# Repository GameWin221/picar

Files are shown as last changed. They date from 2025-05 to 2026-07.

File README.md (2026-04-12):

# picar
Car with autonomous and remote-controlled capabilities controlled by Raspberry Pi 5 and a CH32V003 microcontroller. Features a custom made mainboard PCB responsible for controlling motors, servos and delivering power to the RPi 5.

It is capable of real-time remote control with a gamepad (e.g. XBox One gamepad) alongside a live WebRTC stream from its camera.
Moreover, simple autonomous driving is possible by following an RGB tracking marker.

### Version 3 Early (still the old frame from V2)

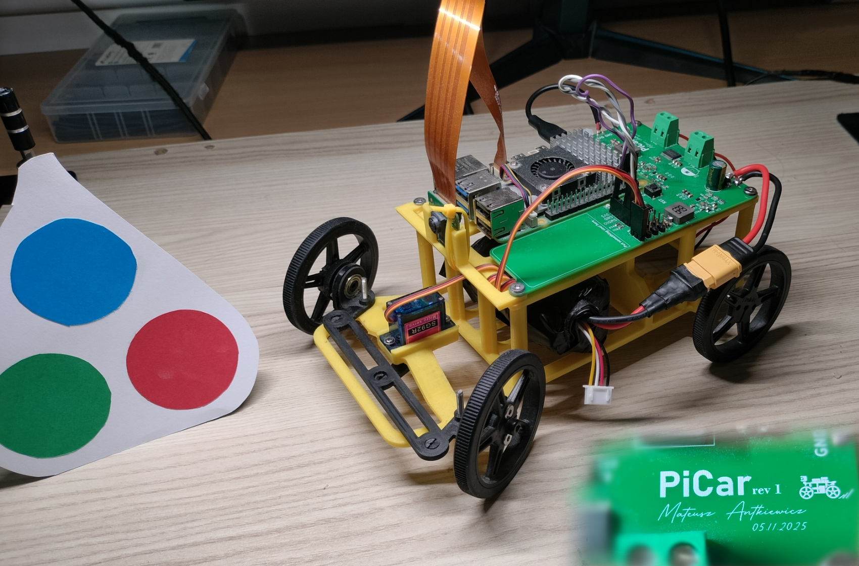
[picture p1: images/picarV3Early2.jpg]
picarV3early1

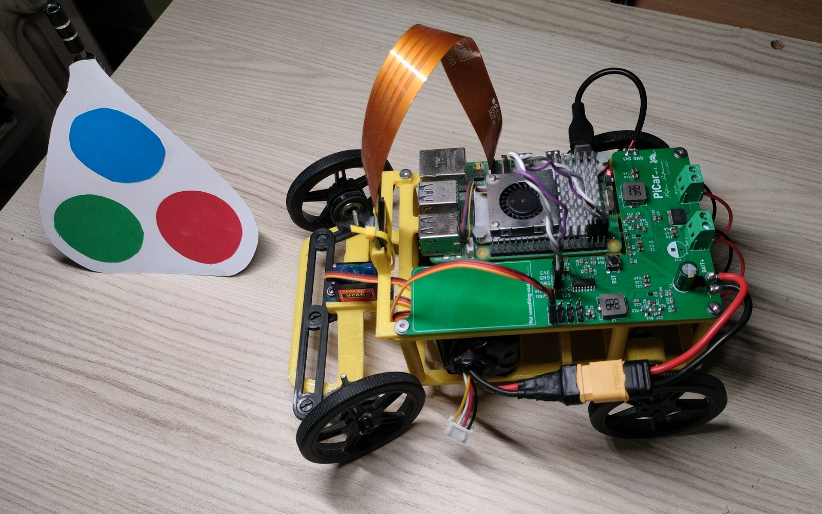
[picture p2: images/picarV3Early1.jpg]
picarV3early2


*PiCar with the tracking marker next to it*

## Future ideas 
- Add a ToF sensor and use it in tandem with the DepthAnything V2 depth estimation model to acquire real (approximated) depth information from the camera.

# Hardware
- Battery pack composed of 3x 18650 cells connected in series. It has both XT60 connector for the main power and 4-pin JST-XH used for balancing.
- SG92R micro servo used for steering
- Raspberry Pi 5 8GB
- Raspberry Pi Camera HD v2 8MPx
- Custom PCB mainboard responsible for controlling motors, servos and delivering power to the RPi 5. (More on that [below](#pcb-mainboard))
- Custom 3D-printed frame and steering system (files available in the "designs" directory)
- 4x 60x8mm black Pololu 1420 wheels
- 2x 6x13x5mm bearings for the front wheels
- 2x N20-BT07 micro 100:1 320RPM 12V motors
- M3 screws used for assembling the frame and wheels together

## PCB mainboard
schematic

*/pcb_main_board/pcb_main_board_schematic.svg*

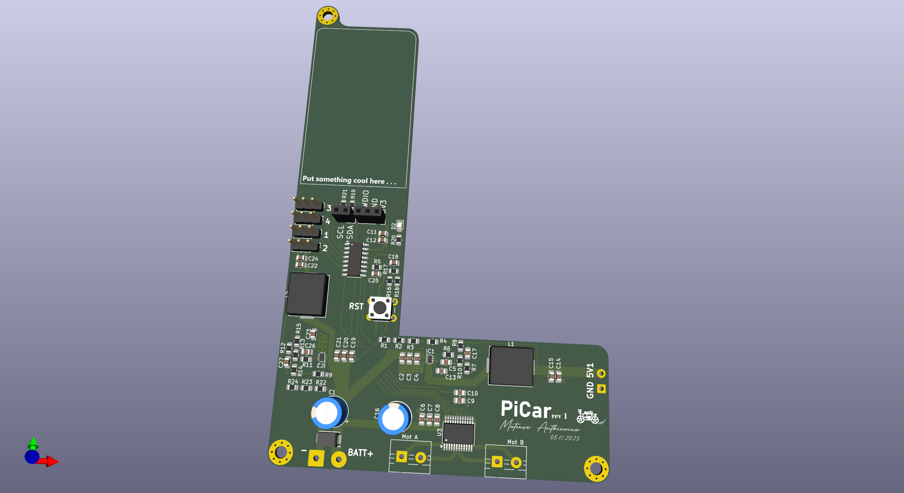
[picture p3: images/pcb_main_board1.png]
render


*/images/pcb_main_board1.png*

### On-board microcontroller

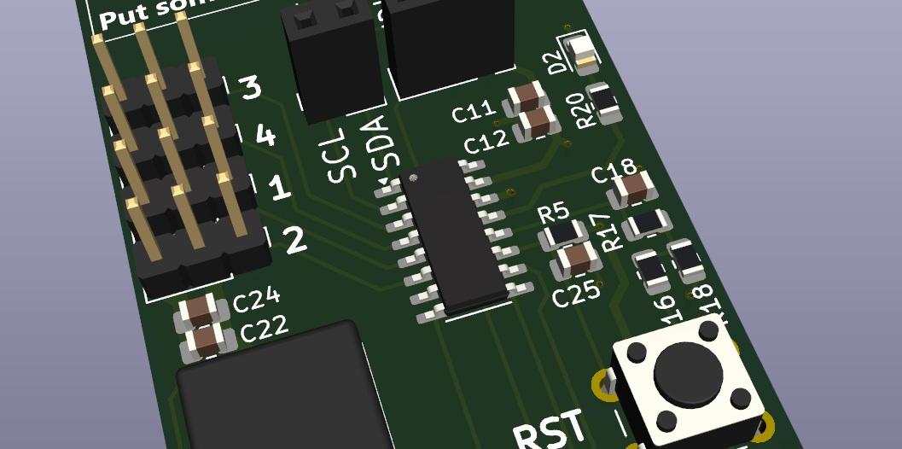
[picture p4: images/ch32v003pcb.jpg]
ch32v003


CH32V003 MCU is the main controller of the whole board. It is responsible for controlling the motor drivers, servo motors and monitoring the battery voltage. It communicates with the Raspberry Pi 5 over I2C.

### Battery to RPi 5 voltage step-down

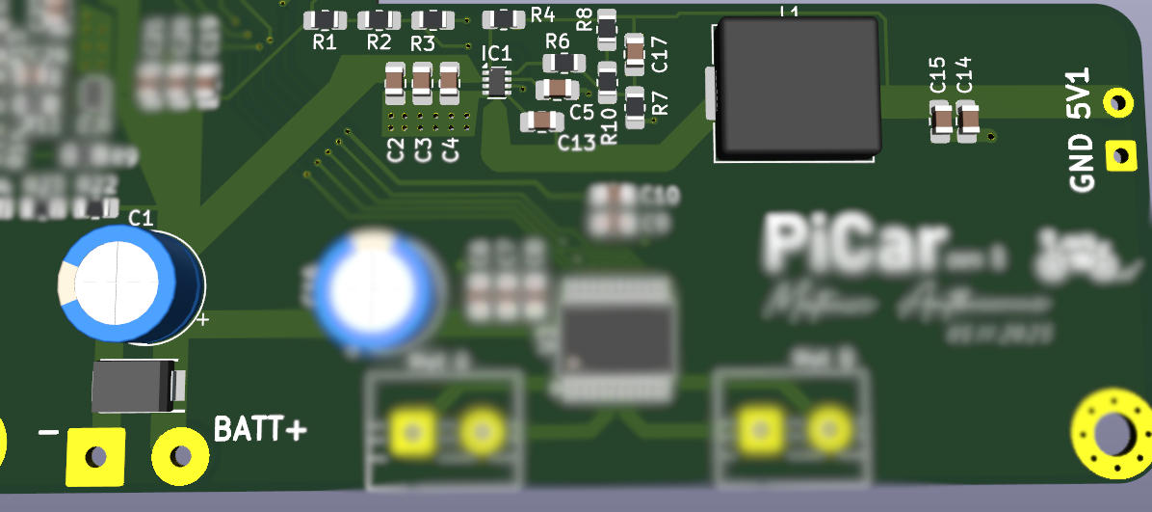
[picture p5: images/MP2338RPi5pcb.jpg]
mp2338


The battery input voltage is first filtered by the input low-ESR capacitor and capped to 15V by a SMBJ15A TVS diode. Then the MP2338 IC is used to reliably step-down the battery voltage from 9V-12.6V range to ~5.1V that is then connected via a USB-C cable to the RPi 5. The MP2338's GND pin is connected to wide copper traces with vias in order to improve cooling.

### Motor control

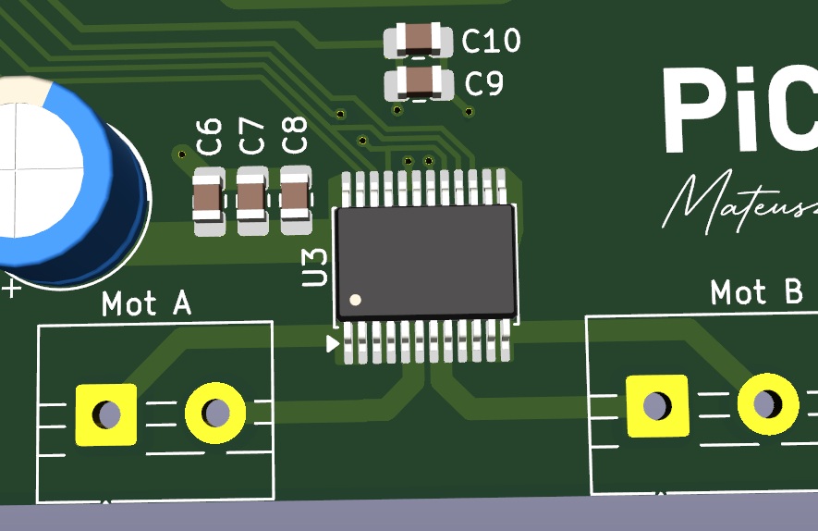
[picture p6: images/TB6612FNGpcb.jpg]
motors


TB6612FNG IC is used to drive both of the main motors. The IC logic is driven by PWM signals generated by the on-board microcontroller. The PWM frequency can be adjusted from the software layer if the user wants to prioritize peak power or to minimize the audible switching noise. The lower the frequency, the more efficient the motors are, but the louder they become.

### Servo control

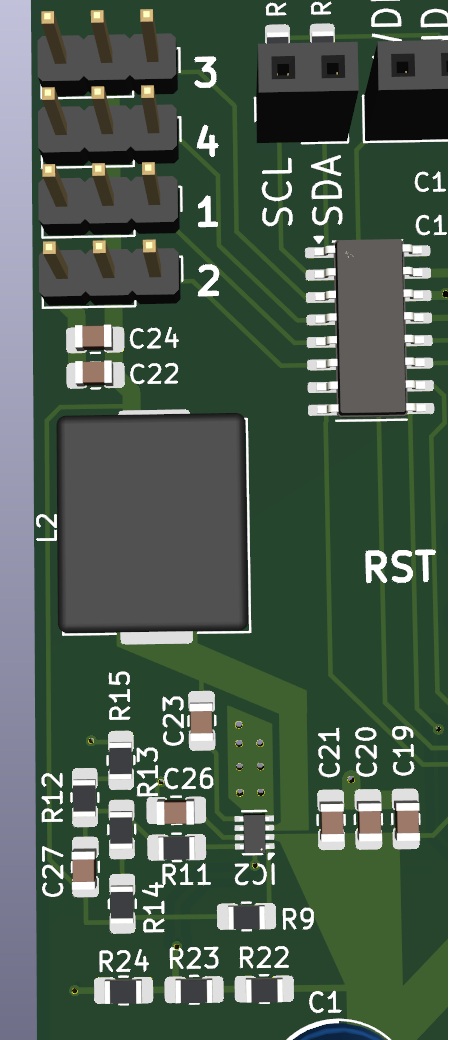
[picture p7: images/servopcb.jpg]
servo


The mainboard is capable of running 4 separate hardware PWM signals at once which are generated by the on-board microcontroller. The servo motors are powered with 4.8V generated by another MP2238 IC configured in the same way as the other one used for powering RPi 5, except for the output voltage. The servo section also has a 3-pin header for each signal channel in order to simplify the connections. There are more servo channels than are currently needed for future-proofing reasons. *e.g. allowing the camera to have adjustable yaw and pitch in the future.*

### Wheels

The front wheels are fastened to their mounts with short M3 screws. Those mounts then clip into the ball bearings, working similarly to LEGO Technic connections. A pin with the correct diameter and side cuts is pushed into the bearing hole and holds firmly enough for normal operation. The rear wheels are press-fitted onto the motor shafts:

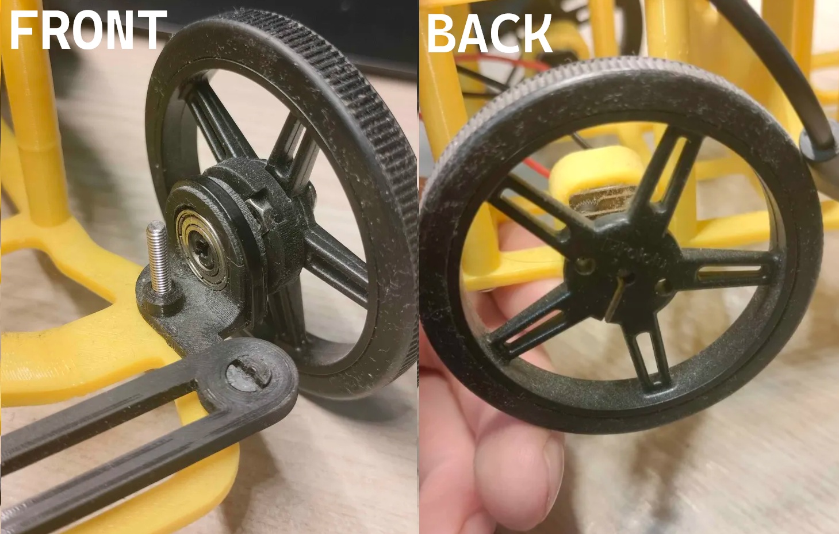
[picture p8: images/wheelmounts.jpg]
frontandback


Front wheel assembly disassembled in Fusion 360:

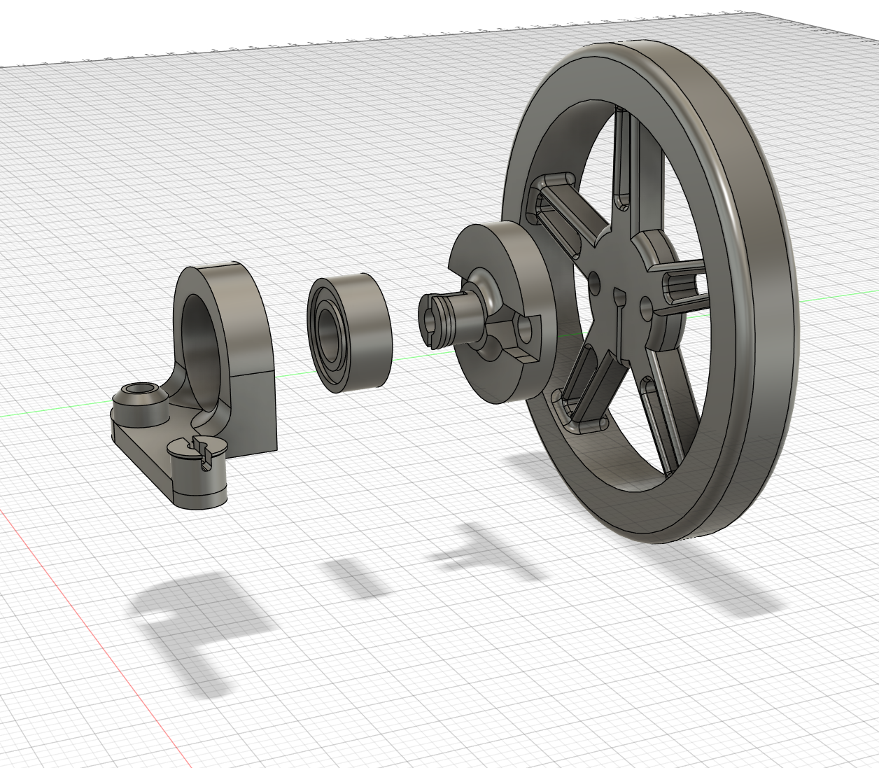
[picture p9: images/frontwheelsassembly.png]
frontwheelassembly


# Software and control

## Frontend
**PiCar** can be controlled through a simple Websockets-based web interface (`/car/software/index.html`). When you run the Python `"Remote Control" main loop` an HTTP server starts up and reveals the visual interface at `http://{raspberry_pi_5_ip}:8000`. There are two sliders that control it but the better (and way cooler) option is to **use a gamepad and control the car this way**. The website automatically detects connected gamepads and lets the user steer by using both triggers for accelerating and braking and the left thumbstick for steering. It is also possible to set the motors PWM switching frequency.

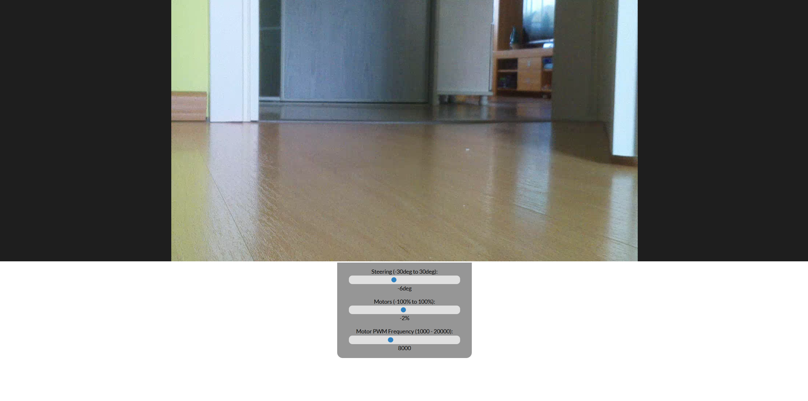
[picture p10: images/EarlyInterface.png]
frontenddemo


There also is a viewport for watching the live feed coming from the camera connected to the RPi 5. The stream source must be a WebRTC source which can be created easily by using [MediaMTX](https://github.com/bluenviron/mediamtx). You can find the working `mediamtx.yml` file I use to enable the stream at `/car/mediamtx.yml`. Once mediamtx starts with my provided config, the camera can be accessed by connecting via WebRTC to `{raspberry_pi_5_ip}:8889/rpi`.

## Vision

Autonomous driving, for now, is a simple computer vision algorithm that searches for a special marker with three key colors: red, green, and blue on the live feed streamed from the Raspberry Pi Camera HD v2 8MPx.

The camera feed is first filtered bilaterally to remove small details and noise in the subsequent marker search. Then gamma is adjusted to increase contrast, and the resulting image is binarized so that the SimpleBlobDetector from the OpenCV library can detect three circles. Finally, the algorithm checks whether the circles are "inside" the potentially found marker—i.e., whether they are not shifted from the averaged center by more than one standard deviation. If they are not, we can be certain that the marker has been found.

Below is a visualization of how the marker is seen by the algorithm:

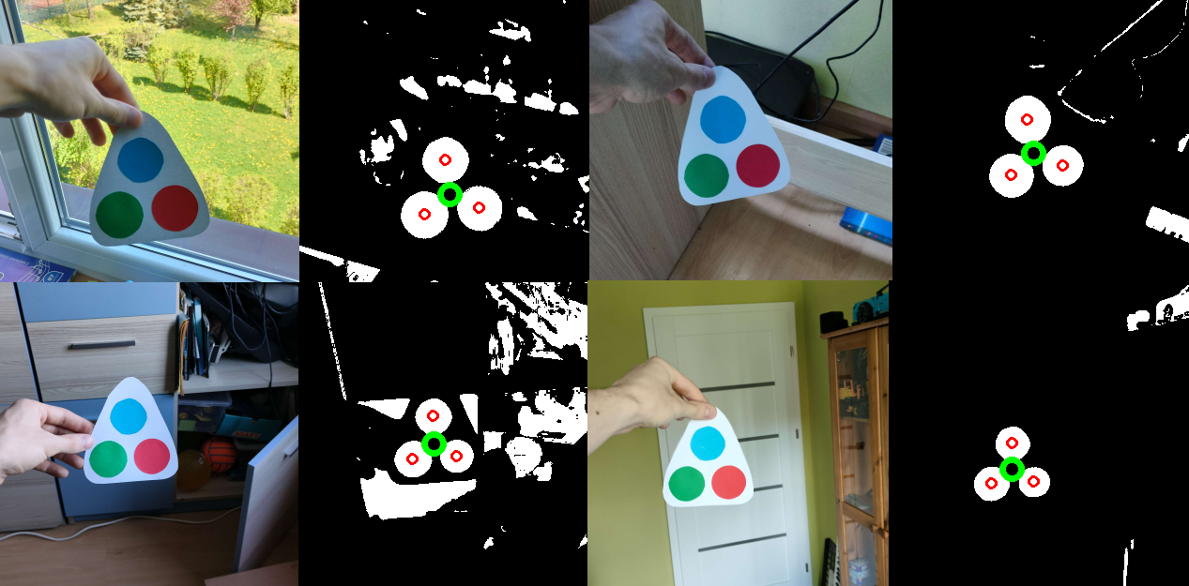
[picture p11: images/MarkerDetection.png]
MarkerDetection


When the marker is found, the vehicle drives forward and turns so that the center of the marker aligns with the center of the camera's view. This is sufficient to effectively track the marker.

### Future Vision Enhancement

I plan to use a ToF distance sensor in tandem with the computer vision model **DepthAnythingV2**, which estimates depth using a single camera. This combination will allow me to acquire approximate (yet sufficiently accurate) distance information of everything visible in the front camera. This data will enable shape detection by contours and autonomous obstacle avoidance.

## Firmware

The CH32V003 microcontroller runs a firmware that acts as a PWM and motor control interface for the Raspberry Pi 5. The firmware exposes a register-based interface over I2C using slave address `0x17`, allowing the RPi to elegantly control all aspects of motor and servo operation.

### I2C Communication Protocol

The firmware operates as an I2C slave that receives write-only commands structured as `[register_id, data_low, data_high]`. Each register controls a specific aspect of the system:

| Register | Purpose | Range |
|---|---|---|
| 1 | TIM1 (servo) frequency | 1 - 48000 Hz |
| 2 | TIM2 (motor) frequency | 1 - 48000 Hz |
| 4-7 | Servo CH1-CH4 duty cycle | 0 - PWM_PERIOD(1000) |
| 10-11 | Motor PWM (right/left) duty cycle | 0 - PWM_PERIOD(1000) |
| 12 | Motor direction control | Bit 0: DIRF, Bit 8: DIRB |

## Building the code

### RPi 5 Python
Configure the virtual environment if you need and run `pip install -r requirements.txt` while being in the `/car/software` directory to download the necessary packages. Downlaod opencv as a standalone package. Once everything is downloaded, run `python main.py` and it should work fine.

#### Enabling the necessary RPi 5 options
To make I2C communication work properly, enable it either with the `raspi-config` command or by manually adding the necessary lines to the `/boot/firmware/config.txt` file:

```
dtparam=i2c_arm=on
dtparam=i2c_arm_baudrate=80000 # or any other as you wish
dtparam=i2s=on
```

Also enable the camera detection in the same way. Here is the line for `/boot/firmware/config.txt`:

```
camera_auto_detect=1
```

### CH32V003 C Firmware
Downloading and building it through MounRiver Studio IDE is the easiest route to go. This repo already has project files that work out of the box when you open them with the IDE. Just press F7 and it should build perfectly fine.

#### Flashing it
You'll need a **WCH LinkE** programmer in order to flash the firmware to the chip. Once you have it, connect GND to GND and the SWDIO pin to the chip's SWIO pin according to its datasheet *(It's pin PD1 for CH32V003A4M6)*. The chip must be powered either from the programmer's voltage pin or externally during flashing.

Now go to MounRiver Studio IDE and press F7 to build your project and then F8 to flash it having the WCH LinkE programmer plugged into your computer at the same time, **note that flashing your code does not rebuild it automatically, you have to remember to press F7 each time.**. You can also change the flashing configuration but it's almost always good to go by default. *(called Download Configuration)*:

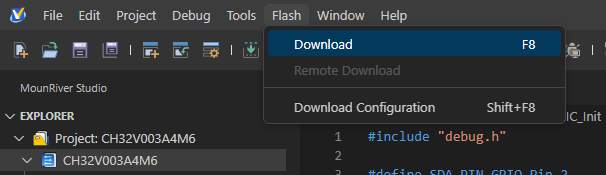
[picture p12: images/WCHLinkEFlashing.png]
wchlinke


Do not press or hold the reset button during flashing (the NRST pin)

# Archive

Take a look at the [PROGRESS.md markdown file](/PROGRESS.md) to see how the project evolved over time.

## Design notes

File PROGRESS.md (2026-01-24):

# Progress over time

## V3 (November 2025 / January 2026)

picarV3early1
picarV3early2

**You can read about it in the main README for as long as it is the newest version.**

## V2 (August 2025)

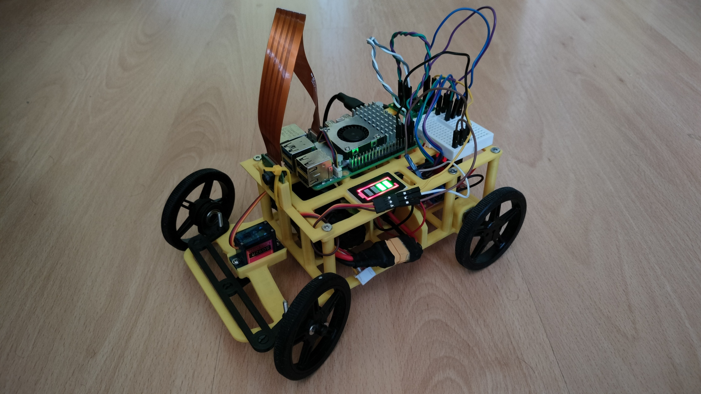
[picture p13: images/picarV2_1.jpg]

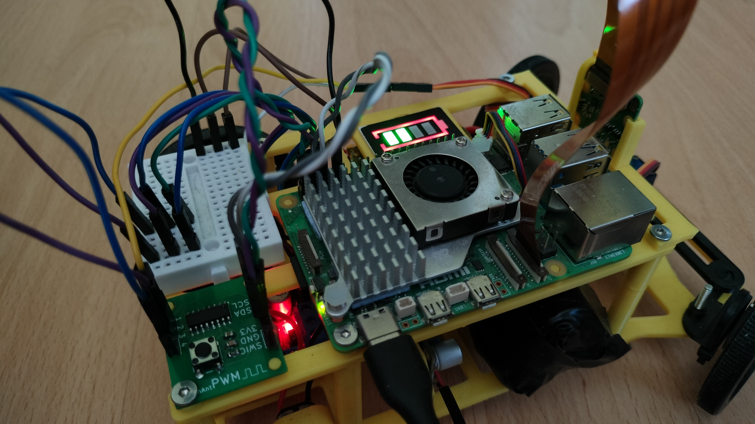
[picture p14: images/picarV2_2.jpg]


### Hardware
- [...] Same as V1 except for:
- Custom PWM control board based on CH32V003 (More on that [below](#ch32v003-mantpwm-pwm-board))
- A small breadboard used only for making the jumper wire connections easier to manage for now. *(I will get rid of it eventually because it doesn't look good)*

### CH32V003 "mAntPWM" PWM Board

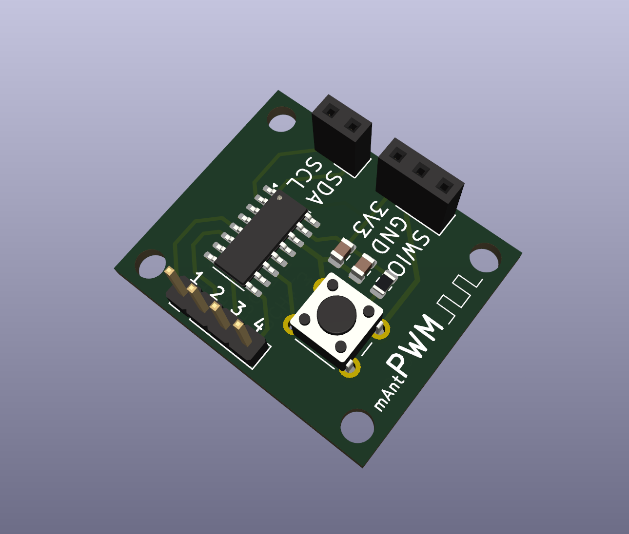
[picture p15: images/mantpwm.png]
mantpwm


*(The KiCad design files are in the `/pwm_board/design` directory)*

The board was designed and created to improve the PWM signal management. Raspberry Pi 5 itself was not enough because it can handle only 2 hardware PWM channels and I needed at least 3 channels so creating the board was both a solution to this problem and a cool sub-project to work on. Before making this board I came up with a temporary solution which you can read about [below](#saving-up-on-pwm-channels-before-the-pwm-board). 

Now I can see some flaws in the design such as wasted PWM outputs (I could've had up to 8 outputs instead of 4) or no on-board pull-up resistors for I2C but the board works as intended so I won't be ordering any new designs for now. 

### RPi 5 <-> mAntPWM coomunication
The RPi 5 communicates with the CH32V003 chip via I2C using a simple protocol documented in `/pwm_board/firmware/CH32V003A4M6/User/main.c`. You can also understand it better by reading the control functions in `/car/software/pwm_board.py`.

## V1 (April 2025)

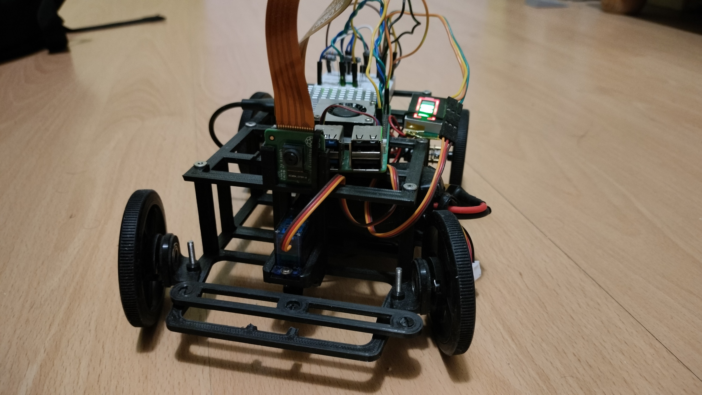
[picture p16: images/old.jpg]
v1pic1

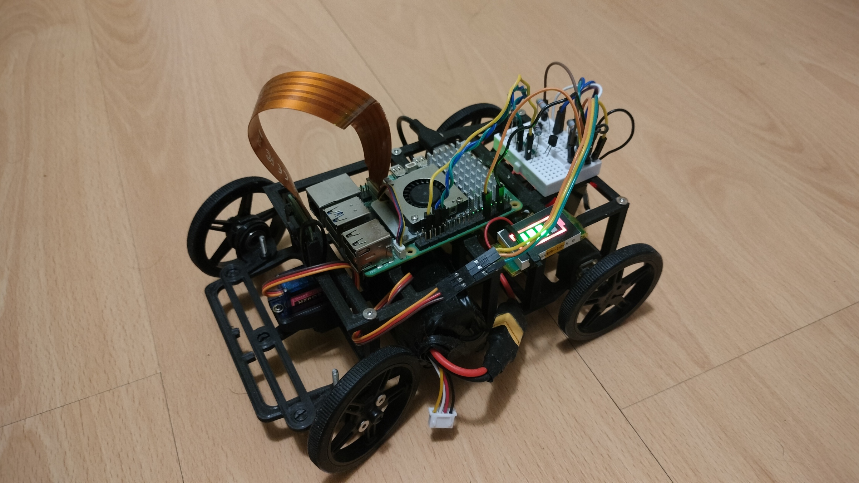
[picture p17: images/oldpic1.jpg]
v1pic2


### Hardware
- Powered by a custom made battery pack composed of 3x 18650 cells connected in series. It has both XT60 connector for the main power and 4-pin JST-XH used for balancing.
- SG92R micro servo for steering
- Raspberry Pi 5 8GB
- Raspberry Pi Camera HD v2 8MPx
- Custom PWM control board based on CH32V003 (More on that [below](#ch32v003-mantpwm-pwm-board))
- LM2596 step-down converter rated for 3A and set to (a bit more than) 5.1V used for powering the Raspberry Pi
- L298N motor driver used for motor control and for generating 5V powering the servo
- Cheap unnamed battery level indicator
- Custom 3D-printed frame and steering system (files available in the "designs" directory)
- 4x 60x8mm black Pololu 1420 wheels
- 2x 6x13x5mm bearings for the front wheels
- 2x N20-BT07 micro 100:1 320RPM 12V motors
- M3 screws used for assembling the frame and wheels together
- Breadboard with two BC337 transistors and required resistors.

### Saving up on PWM channels before the PWM board
Raspberry Pi 5 can generate only 2 channels of hardware PWM at once and I had to provide at least 3 PWM signals - one to control the servo, one for driving forward and one for driving backward. Since I didn't want to use software-based PWM I had to somehow cut down the number of signals. The obvious choice was to use only one PWM signal for the motors and to control the direction with digital outputs. I did it simply by switching the single PWM signal with two transistors going into separate inputs in the motor driver. 

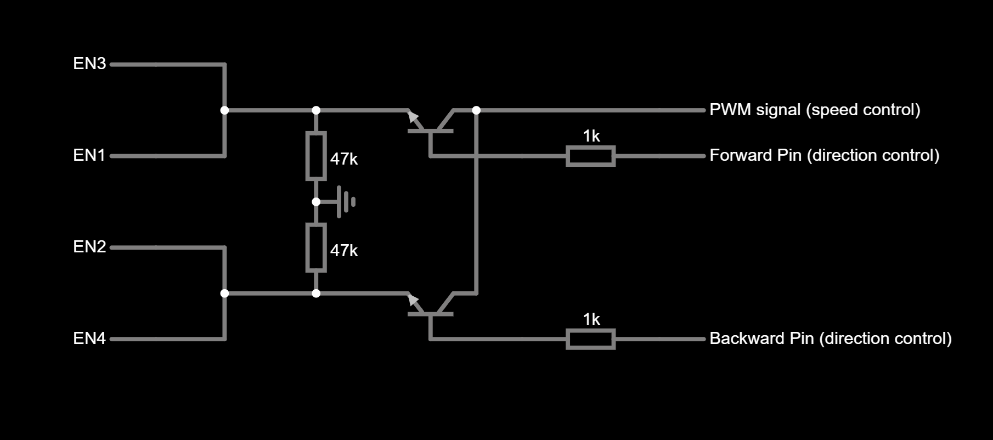
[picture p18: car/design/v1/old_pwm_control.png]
oldpwm


*Irl it was a messy setup on a breadboard as you can imagine.*

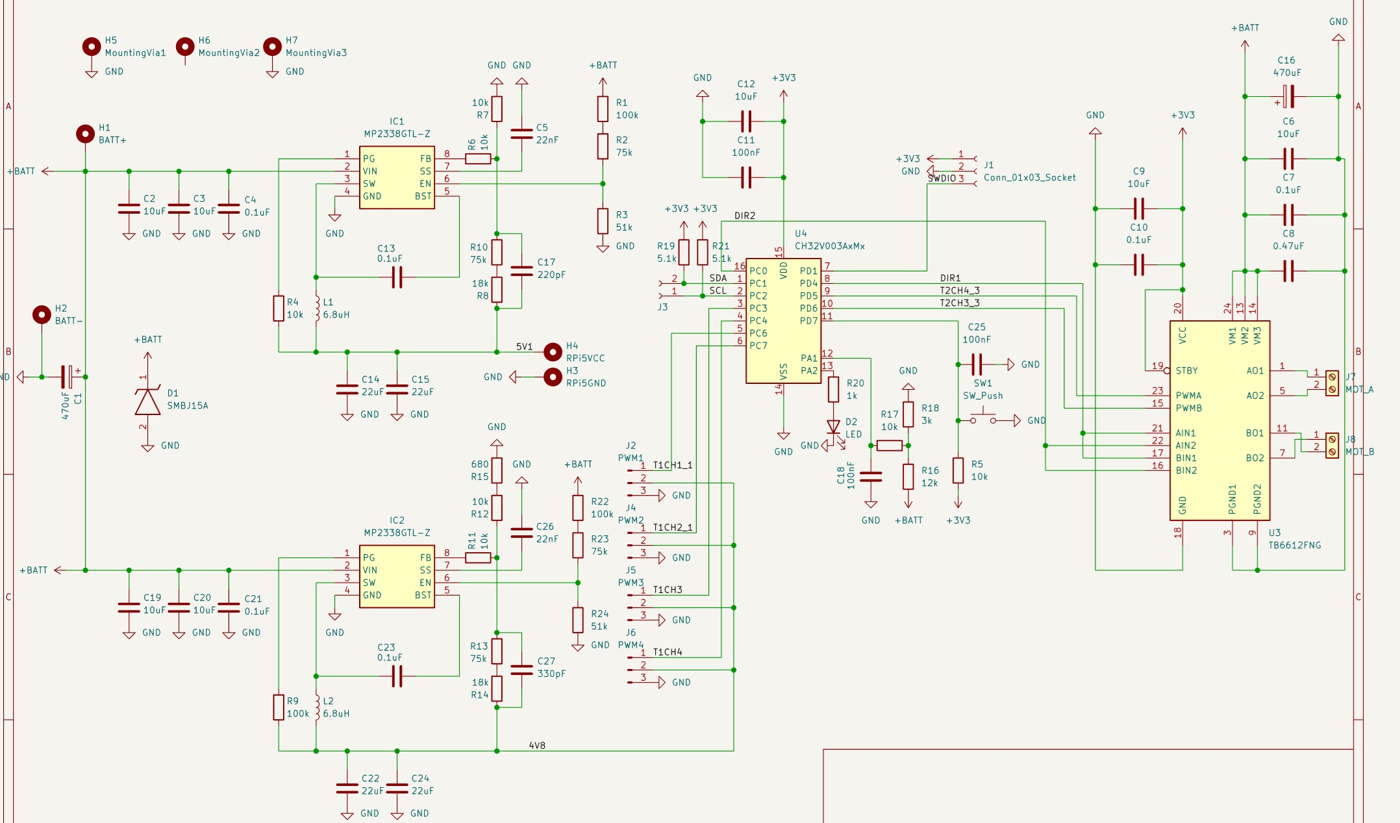
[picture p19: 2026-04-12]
images/schematicimage.jpg

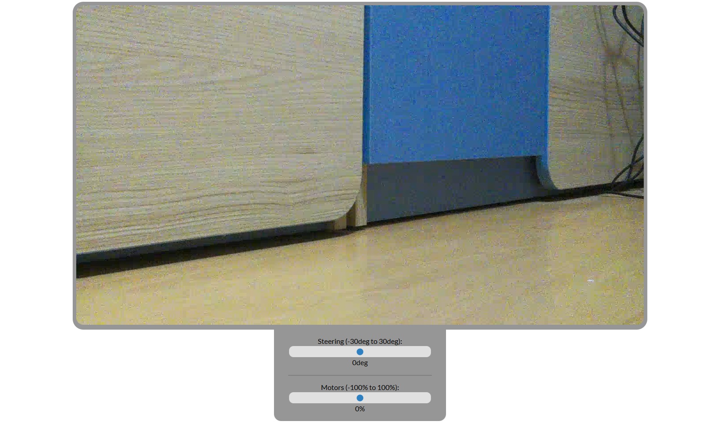
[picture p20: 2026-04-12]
images/WebInterface.jpg

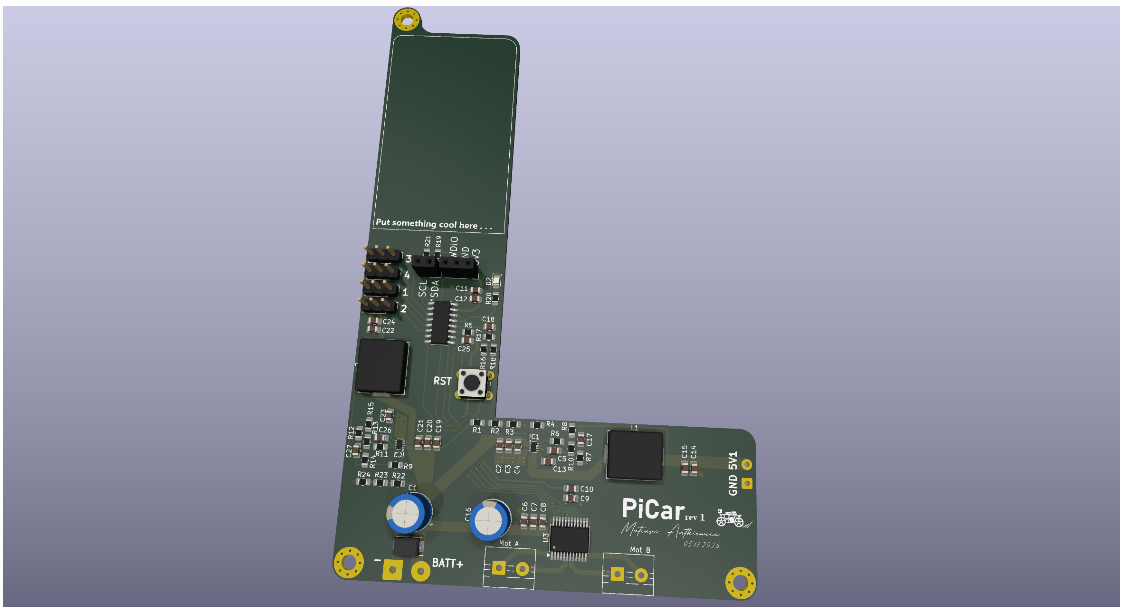
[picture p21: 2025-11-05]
images/pcb_main_board_rt1.png

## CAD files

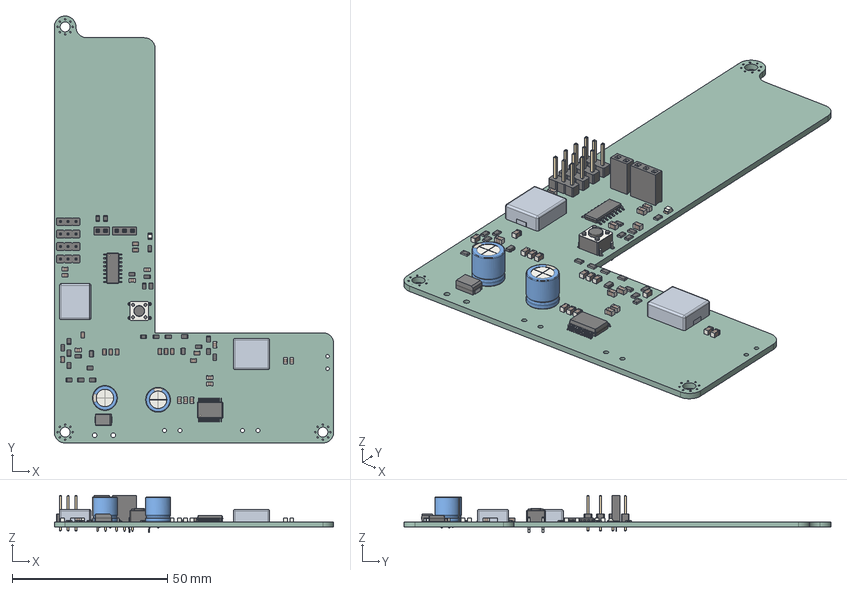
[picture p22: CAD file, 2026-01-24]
new_pcb_main_board/design/pcb_main_board.step
90.0 x 137.5 x 12.0 mm
C_0805_2012Metric x 25
R_0805_2012Metric x 24
CP_Radial_D8.0mm_P3.50mm x 2
PinHeader_1x03_P2.54mm_Vertical x 4
SW_PUSH_6mm
SOT-583-8 x 2
pcb_main_board 1.29.1 x 2
SSOP-24_5.3x8.2mm_P0.65mm
SOP-16_3.9x9.9mm_P1.27mm
FilletPin1
FilletPin2
PinSocket_1x03_P2.54mm_Vertical
LED_0805_2012Metric
PinSocket_1x02_P2.54mm_Vertical
pcb_main_board_PCB

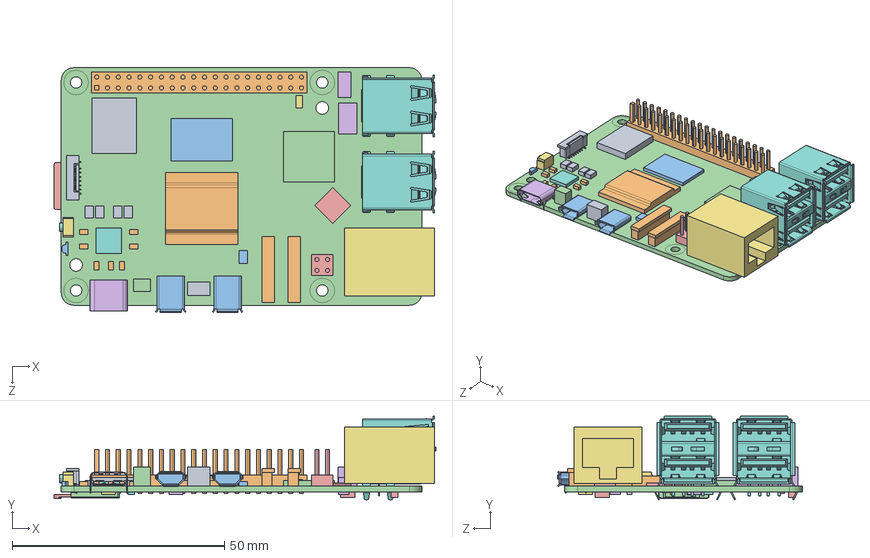
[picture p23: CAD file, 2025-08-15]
car/design/RaspberryPi5.step
90.0 x 19.8 x 57.7 mm
PCB_for REF 060923
GPIO Header for REF
Micro HDMI for REF x 2
SD CARD for REF
USB-C for REF
RJ45 for REF
USB for REF x 2
PCIe for REF
CAM-DISP for REF x 2
LED for REF
BAT Header for REF
PoE Header for REF
FAN Header for REF
SWITCH for REF
UART for REF

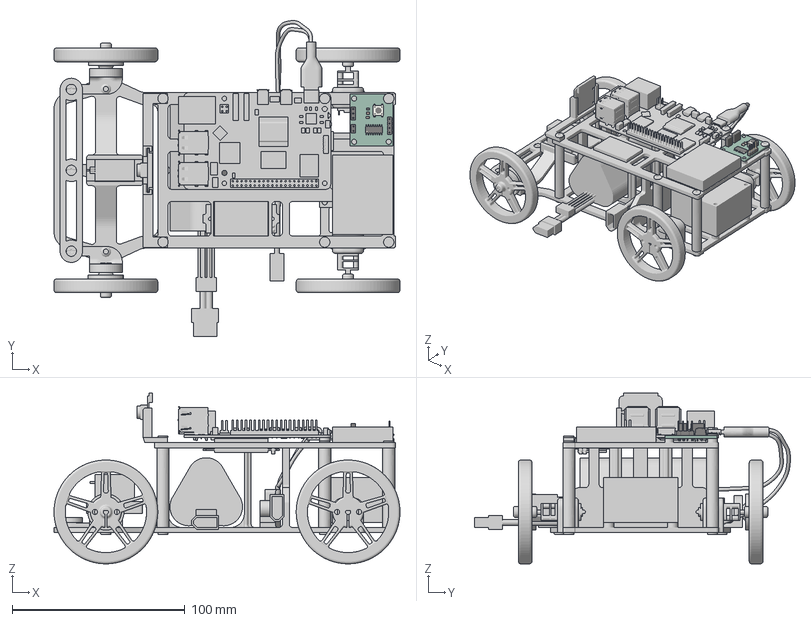
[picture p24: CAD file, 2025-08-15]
car/design/v2/picar.3mf
200.0 x 182.6 x 98.7 mm
Battery3S
BatteryDisplay
BearingFL
BearingFR
BottomFrame
Breadboard
Camera
CameraHandle
Driver
M3Screw1 (1) (1) (1) (1)
M3Screw1 (1) (1) (1)
M3Screw1 (1) (1)
M3Screw1 (1)
M3Screw1
M3Screw2 (1) (1) (1) (1)
M3Screw2 (1) (1) (1)
M3Screw2 (1) (1)
M3Screw2 (1)
M3Screw2
M3Screw3
M3Screw4
M3Screw5
M3Screw6
MotorBL
MotorBR
PowerCable1
PowerCable2
PowerConverter1
Servo
ServoArm
Standoff1 (1)
Standoff1
Standoff2 (1) (1)
Standoff2
Standoff3 (1)
Standoff3
SteerArmFL
SteerArmFR
SteerLinkage
TopFrame
USB_C_Connector
WheelBL
WheelBR
WheelFL
WheelFR
WheelMountFL
WheelMountFR

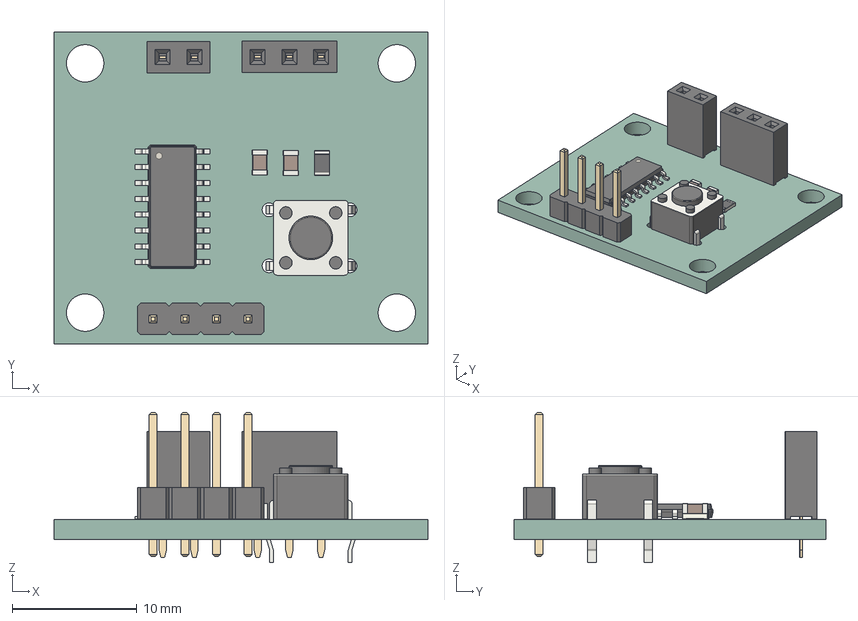
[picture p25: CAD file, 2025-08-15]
pwm_board/design/servo_controller.step
30.0 x 25.0 x 12.0 mm
C_0805_2012Metric x 2
PinSocket_1x02_P254mm_Vertical
PinSocket_1x03_P254mm_Vertical
PinHeader_1x04_P254mm_Vertical
SW_PUSH_6mm
SOP-16_3.9x9.9mm_P1.27mm
R_0805_2012Metric
servo_controller_PCB

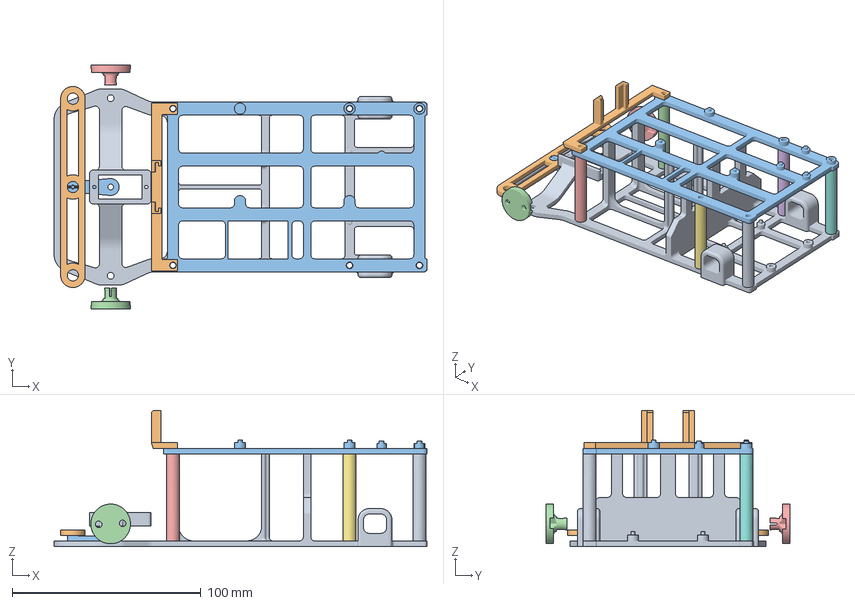
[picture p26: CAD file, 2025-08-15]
car/design/v2/picar_only_3d_printable.3mf
197.5 x 129.0 x 72.1 mm
BottomFrame
CameraHandle
ServoArm
Standoff1 (1)
Standoff1
Standoff2 (1) (1)
Standoff2
Standoff3 (1)
Standoff3
SteerLinkage
TopFrame
WheelMountFL
WheelMountFR

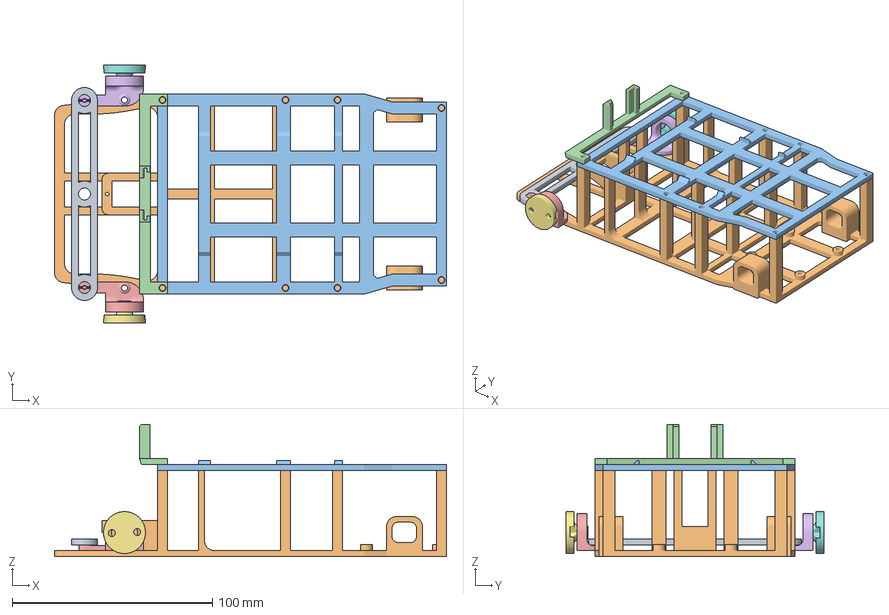
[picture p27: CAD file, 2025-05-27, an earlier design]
car/design/v1/picar_only_3d_printable.3mf
196.0 x 129.0 x 66.1 mm
SteerArmFL
SteerArmFR
WheelMountFL
WheelMountFR (1)

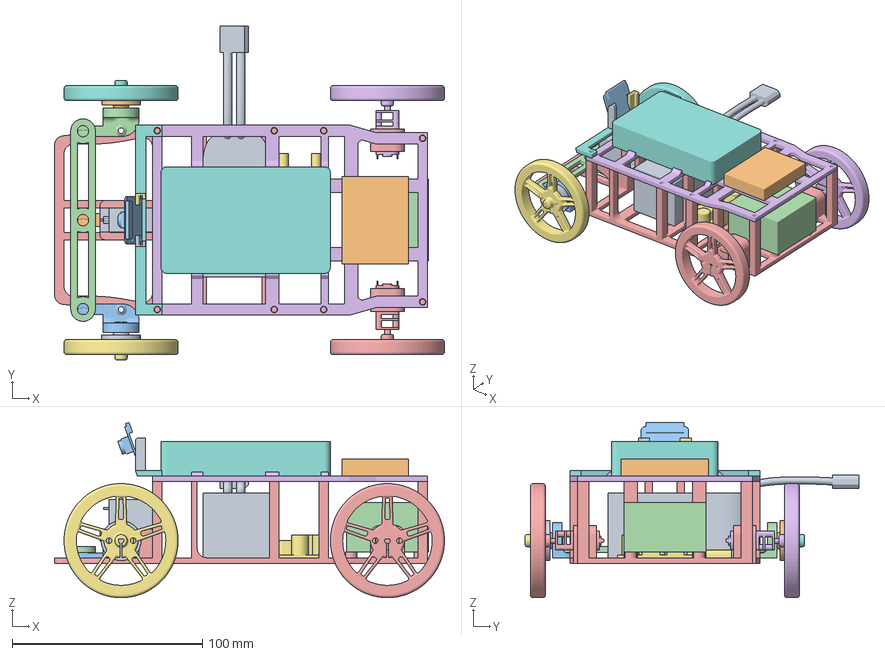
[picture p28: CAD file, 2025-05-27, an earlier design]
car/design/v1/picar.3mf
205.0 x 175.5 x 92.2 mm
Battery
BearingFL
BearingFR
Breadboard
Camera
Driver
MotorBL
MotorBR
PowerConverter (1)
RaspberryPi
Servo
ServoArm
SteerArmFL
SteerArmFR
WheelBL
WheelBR
WheelFL
WheelFR
WheelMountFL
WheelMountFR (1)

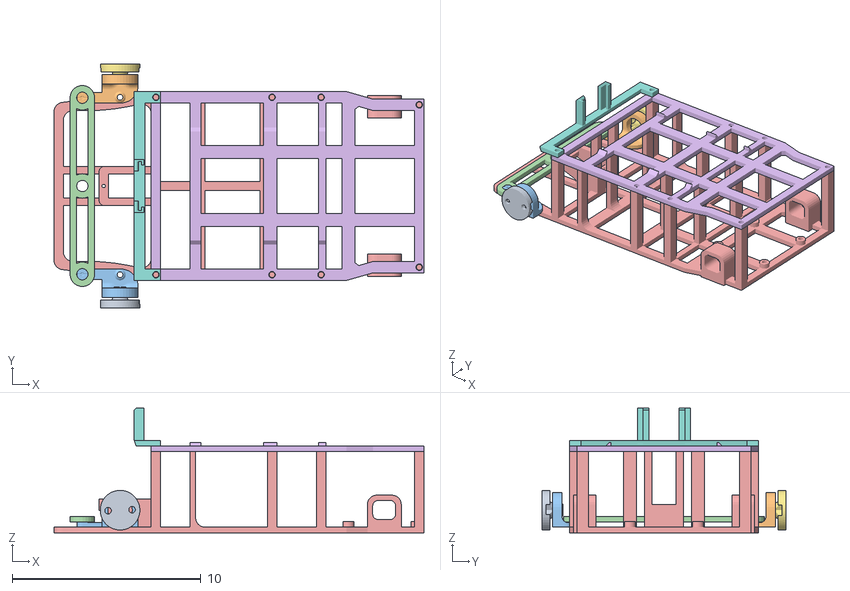
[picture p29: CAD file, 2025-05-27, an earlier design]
car/design/v1/picar_all_3d_printable.obj
19.6 x 12.9 x 6.61
WheelMountFL
SteerArmFR
SteerArmFL
WheelMountFR (1)

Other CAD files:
car/design/v1/picar.f3d
car/design/v1/picar.obj
car/design/v2/picar.f3d
car/design/v2/picar.obj
car/design/v2/picar_only_3d_printable.obj
new_pcb_main_board/design/pcb_main_board.stl

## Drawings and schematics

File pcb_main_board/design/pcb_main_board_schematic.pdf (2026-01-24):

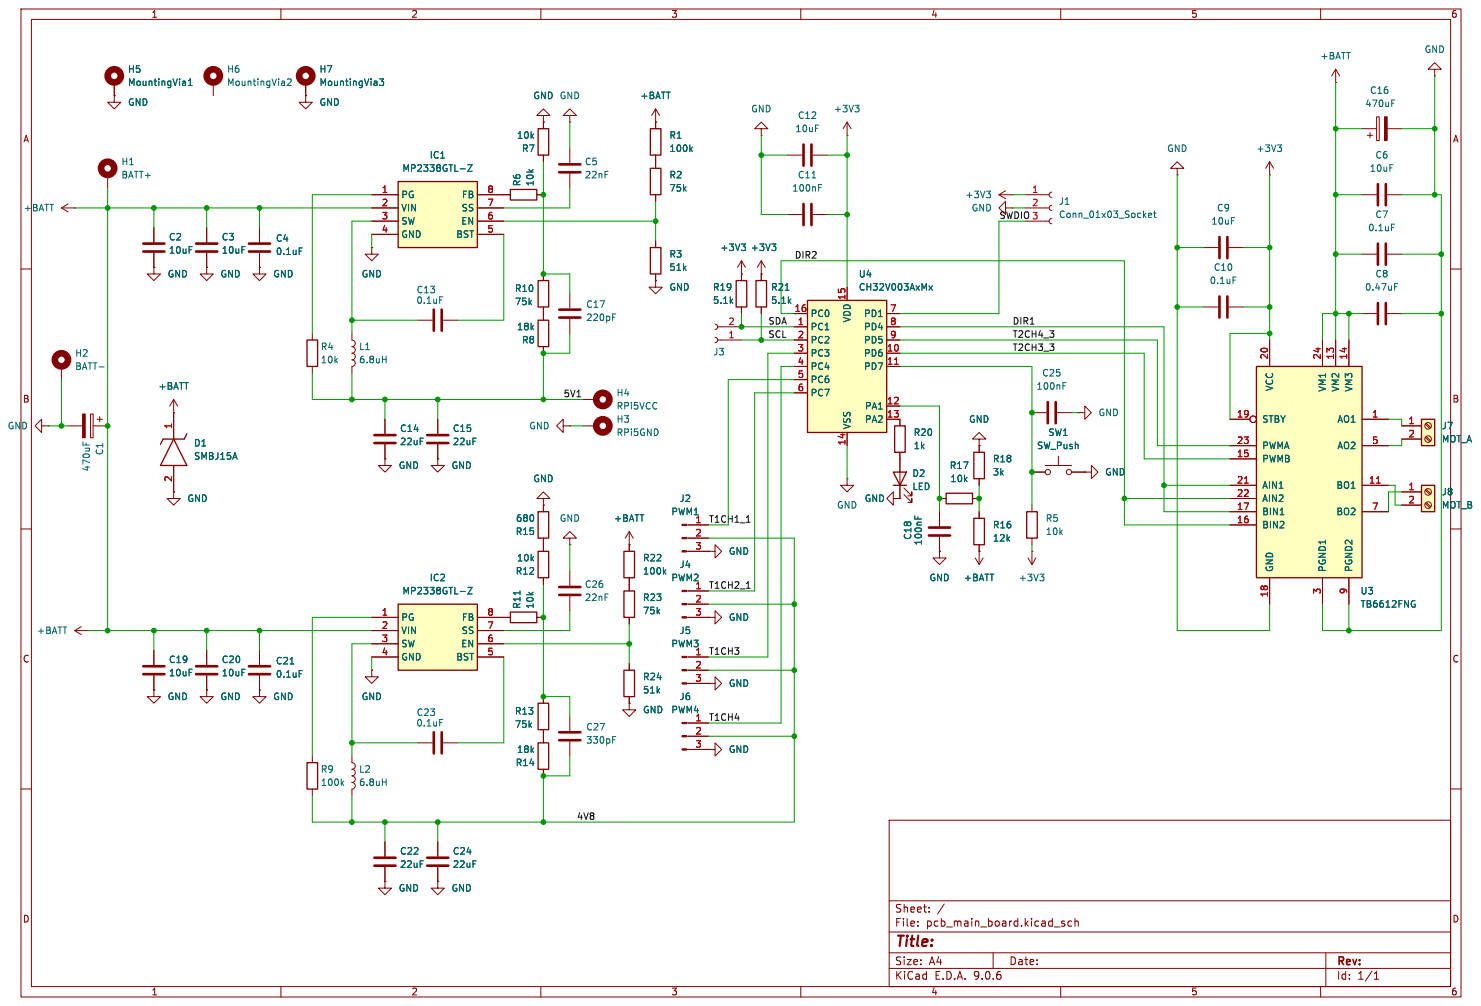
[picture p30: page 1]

Id: 1/1 Title: File: pcb_main_board.kicad_sch Sheet: /

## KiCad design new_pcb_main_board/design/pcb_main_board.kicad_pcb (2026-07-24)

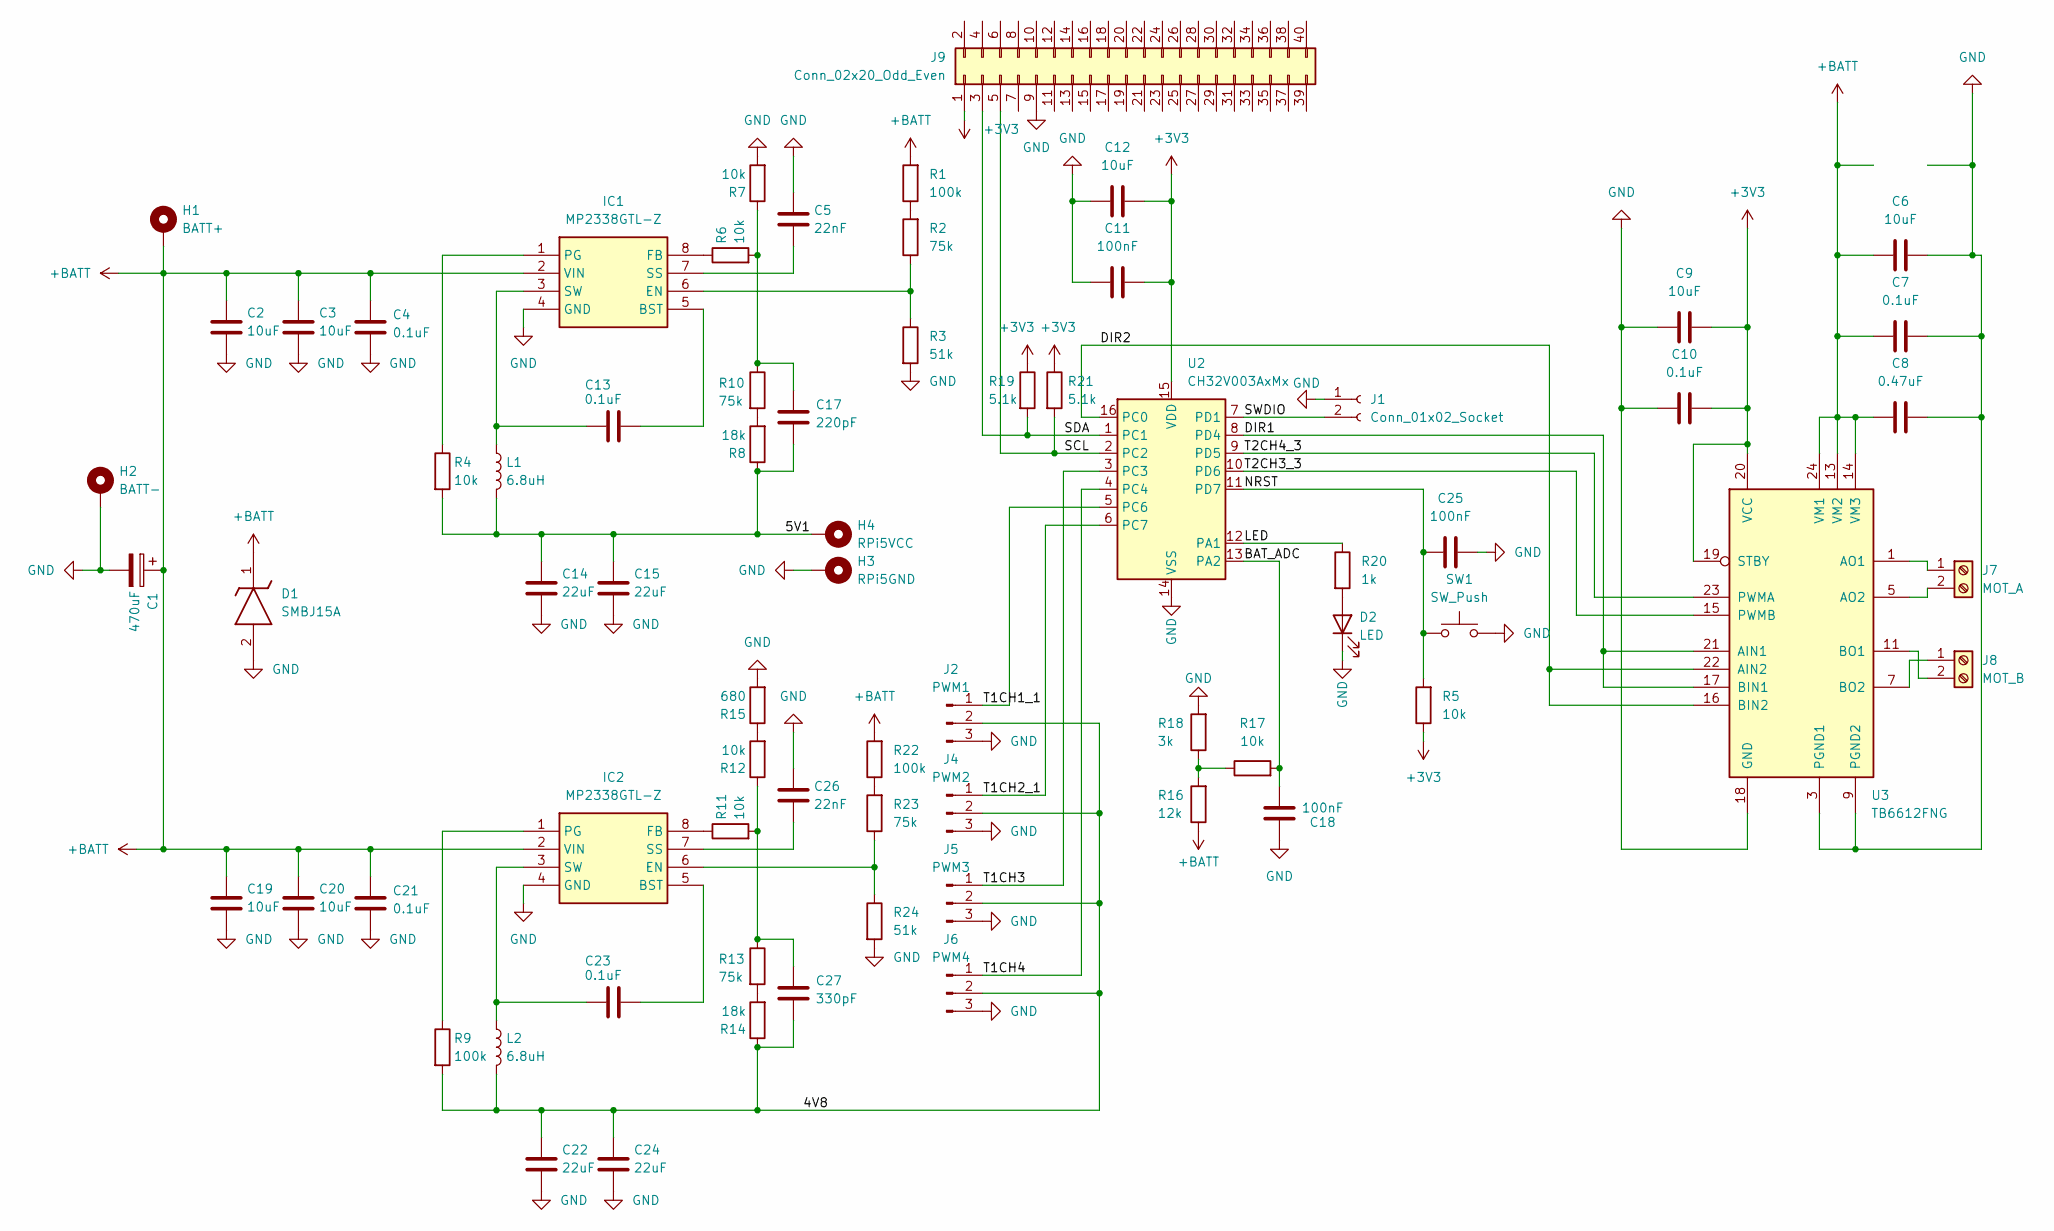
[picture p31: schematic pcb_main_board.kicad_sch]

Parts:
C1: 470uF; CP_Radial_D8.0mm_P3.50mm
C2, C3, C6, C9, C12, C19, C20: 10uF; C_0805_2012Metric
C4, C7, C10, C13, C21, C23: 0.1uF; C_0805_2012Metric
C5, C26: 22nF; C_0805_2012Metric
C8: 0.47uF; C_0805_2012Metric
C11, C18, C25: 100nF; C_0805_2012Metric
C14, C15, C22, C24: 22uF; C_0805_2012Metric_Pad1.18x1.45mm_HandSolder
C17: 220pF; C_0805_2012Metric
C27: 330pF; C_0805_2012Metric
D1: SMBJ15A; DIOM5436X244N; Mouser Part Number 78-SMBJ15A
D2: LED; LED_0805_2012Metric_Pad1.15x1.40mm_HandSolder
H1: BATT+; SolderWire-1sqmm_1x01_D1.4mm_OD3.9mm
H2: BATT-; SolderWire-1sqmm_1x01_D1.4mm_OD3.9mm
H3: RPi5GND; SolderWire-0.5sqmm_1x01_D0.9mm_OD2.3mm
H4: RPi5VCC; SolderWire-0.5sqmm_1x01_D0.9mm_OD2.3mm
IC1, IC2: MP2338GTL-Z; SOT-583-8; Mouser Part Number 946-MP2338GTL-Z
J1: Conn_01x02_Socket; PinSocket_1x02_P2.54mm_Vertical
J2: PWM1; PinHeader_1x03_P2.54mm_Vertical
J4: PWM2; PinHeader_1x03_P2.54mm_Vertical
J5: PWM3; PinHeader_1x03_P2.54mm_Vertical
J6: PWM4; PinHeader_1x03_P2.54mm_Vertical
J7: MOT_A; TerminalBlock_MaiXu_MX126-5.0-02P_1x02_P5.00mm
J8: MOT_B; TerminalBlock_MaiXu_MX126-5.0-02P_1x02_P5.00mm
J9: Conn_02x20_Odd_Even; PinSocket_2x20_P2.54mm_Vertical
L1, L2: 6.8uH; L_Chilisin_BMRF00101040
R1, R9, R22: 100k; R_0805_2012Metric
R2, R10, R13, R23: 75k; R_0805_2012Metric
R3, R24: 51k; R_0805_2012Metric
R4, R5, R6, R7, R11, R12, R17: 10k; R_0805_2012Metric
R8, R14: 18k; R_0805_2012Metric
R15: 680; R_0805_2012Metric
R16: 12k; R_0805_2012Metric
R18: 3k; R_0805_2012Metric
R19, R21: 5.1k; R_0805_2012Metric
R20: 1k; R_0805_2012Metric
SW1: SW_Push; SW_PUSH_6mm
U2: CH32V003AxMx; STC_SOP-16_3.9x9.9mm_P1.27mm
U3: TB6612FNG; SSOP-24_5.3x8.2mm_P0.65mm

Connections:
+3V3: C9.2, C10.2, C11.2, C12.2, J9.1, R5.1, R19.1, R21.1, U2.15 (VDD), U3.19 (STBY), U3.20 (VCC)
+BATT: C1.1, C2.1, C3.1, C4.1, C6.1, C7.1, C8.1, C19.1, C20.1, C21.1, D1.1 (K), H1.1, IC1.2 (VIN), IC2.2 (VIN), R1.2, R16.1, R22.2, U3.13 (VM2), U3.14 (VM3), U3.24 (VM1)
/4V8: C22.1, C24.1, C27.2, J2.2, J4.2, J5.2, J6.2, L2.2, R9.2, R14.1
/5V1: C14.1, C15.1, C17.2, H4.1, L1.2, R4.2, R8.1
/BAT_ADC: C18.2, R17.2, U2.13 (PA2)
/DIR1: U2.8 (PD4), U3.17 (BIN1), U3.21 (AIN1)
/DIR2: U2.16 (PC0), U3.16 (BIN2), U3.22 (AIN2)
/LED: R20.1, U2.12 (PA1)
/NRST: C25.1, R5.2, SW1.1, U2.11 (PD7)
/SCL: J9.5, R21.2, U2.2 (PC2)
/SDA: J9.3, R19.2, U2.1 (PC1)
/SWDIO: J1.2, U2.7 (PD1)
/T1CH1_1: J2.1, U2.5 (PC6)
/T1CH2_1: J4.1, U2.6 (PC7)
/T1CH3: J5.1, U2.3 (PC3)
/T1CH4: J6.1, U2.4 (PC4)
/T2CH3_3: U2.10 (PD6), U3.15 (PWMB)
/T2CH4_3: U2.9 (PD5), U3.23 (PWMA)
GND: C1.2, C2.2, C3.2, C4.2, C5.1, C6.2, C7.2, C8.2, C9.1, C10.1, C11.1, C12.1, C14.2, C15.2, C18.1, C19.2, C20.2, C21.2, C22.2, C24.2, C25.2, C26.1, D1.2 (A), D2.1 (K), H2.1, H3.1, IC1.4 (GND), IC2.4 (GND), J1.1, J2.3, J4.3, J5.3, J6.3, J9.9, R3.2, R7.2, R15.2, R18.2, R24.2, SW1.2, U2.14 (VSS), U3.3 (PGND1), U3.4 (PGND1), U3.9 (PGND2), U3.10 (PGND2), U3.18 (GND)
unnamed: C17.1, R6.2, R7.1, R10.1
unnamed: C27.1, R11.2, R12.1, R13.1
unnamed: D2.2 (A), R20.2
unnamed: C13.2, IC1.5 (BST)
unnamed: IC1.6 (EN), R2.1, R3.1
unnamed: IC1.8 (FB), R6.1
unnamed: IC1.1 (PG), R4.1
unnamed: C5.2, IC1.7 (SS)
unnamed: C13.1, IC1.3 (SW), L1.1
unnamed: C23.2, IC2.5 (BST)
unnamed: IC2.6 (EN), R23.1, R24.1
unnamed: IC2.8 (FB), R11.1
unnamed: IC2.1 (PG), R9.1
unnamed: C26.2, IC2.7 (SS)
unnamed: C23.1, IC2.3 (SW), L2.1
unnamed: J7.1, U3.1 (AO1), U3.2 (AO1)
unnamed: J7.2, U3.5 (AO2), U3.6 (AO2)
unnamed: J8.1, U3.7 (BO2), U3.8 (BO2)
unnamed: J8.2, U3.11 (BO1), U3.12 (BO1)
unnamed: R1.1, R2.2
unnamed: R8.2, R10.2
unnamed: R12.2, R15.1
unnamed: R13.2, R14.2
unnamed: R16.2, R17.1, R18.1
unnamed: R22.1, R23.2

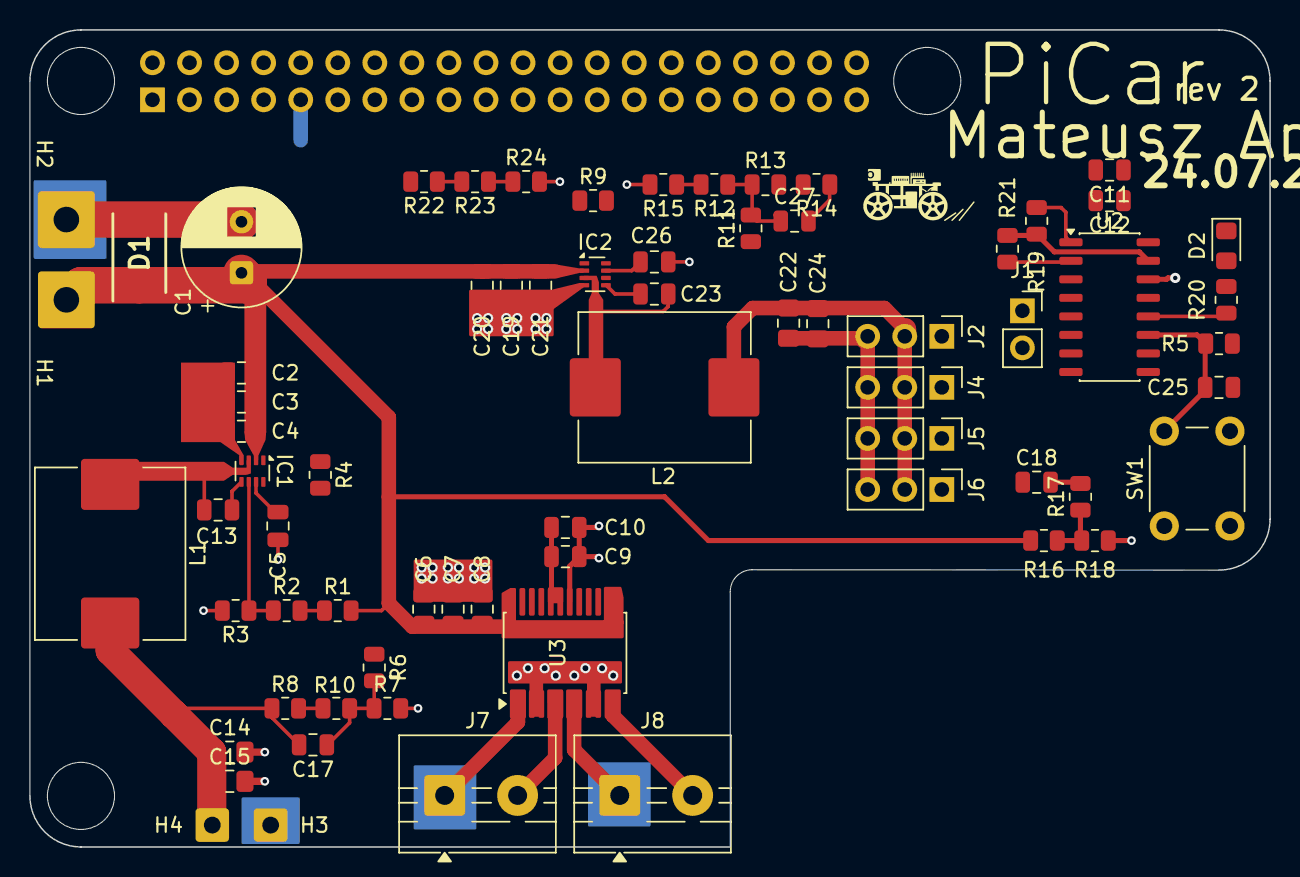
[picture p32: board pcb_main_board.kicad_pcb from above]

Board: 2 copper layers, 85.0 x 56.0 mm, 71 parts (1 on the bottom side), 44 nets.

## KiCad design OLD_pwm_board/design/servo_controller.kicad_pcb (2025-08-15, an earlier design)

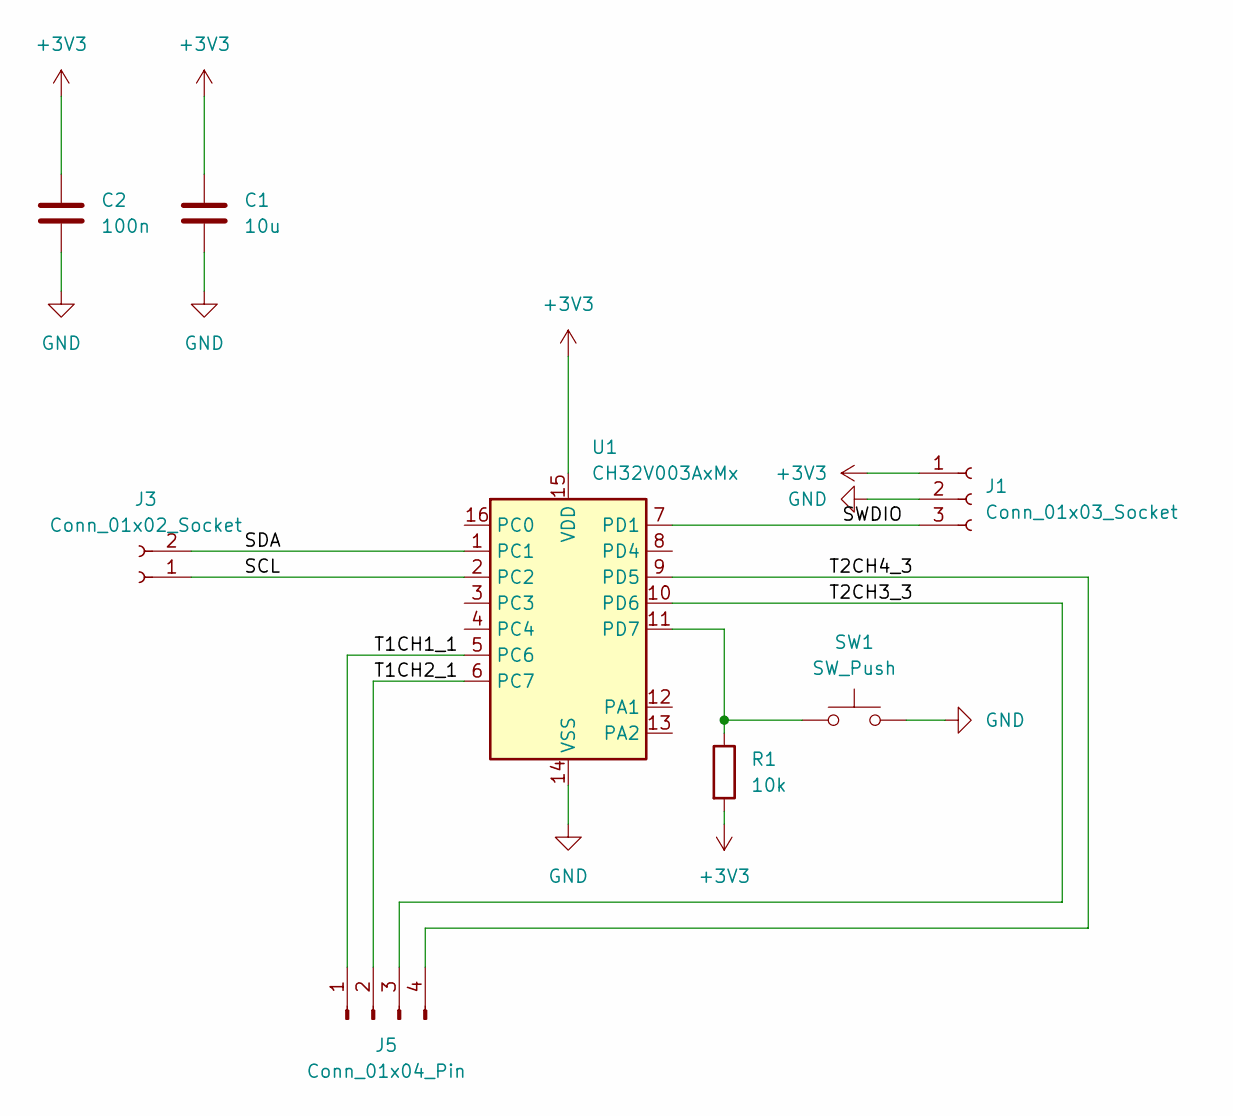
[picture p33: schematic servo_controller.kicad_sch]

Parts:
C1: 10u; C_0805_2012Metric
C2: 100n; C_0805_2012Metric
J1: Conn_01x03_Socket; PinSocket_1x03_P2.54mm_Vertical
J3: Conn_01x02_Socket; PinSocket_1x02_P2.54mm_Vertical
J5: Conn_01x04_Pin; PinHeader_1x04_P2.54mm_Vertical
R1: 10k; R_0805_2012Metric
SW1: SW_Push; SW_PUSH_6mm
U1: CH32V003AxMx; SOP-16_3.9x9.9mm_P1.27mm

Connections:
+3V3: C1.1, C2.1, J1.1, R1.2, U1.15 (VDD)
/SCL: J3.1, U1.2 (PC2)
/SDA: J3.2, U1.1 (PC1)
/SWDIO: J1.3, U1.7 (PD1)
/T1CH1_1: J5.1, U1.5 (PC6)
/T1CH2_1: J5.2, U1.6 (PC7)
/T2CH3_3: J5.3, U1.10 (PD6)
/T2CH4_3: J5.4, U1.9 (PD5)
GND: C1.2, C2.2, J1.2, SW1.2, U1.14 (VSS)
unnamed: R1.1, SW1.1, U1.11 (PD7)

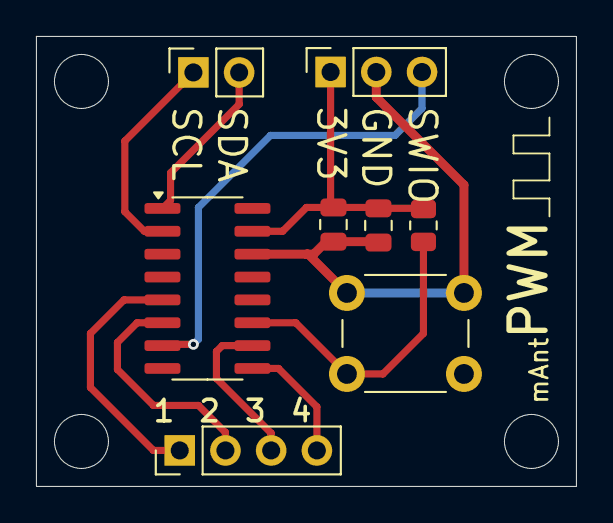
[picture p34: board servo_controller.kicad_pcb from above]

Board: 2 copper layers, 30.0 x 25.0 mm, 8 parts (0 on the bottom side), 10 nets.

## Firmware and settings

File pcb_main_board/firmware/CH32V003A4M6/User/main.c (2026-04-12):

#include "debug.h"

#define SDA_PIN GPIO_Pin_1
#define SCL_PIN GPIO_Pin_2

#define SERVO_CH1_PIN GPIO_Pin_6
#define SERVO_CH2_PIN GPIO_Pin_7
#define SERVO_CH3_PIN GPIO_Pin_3
#define SERVO_CH4_PIN GPIO_Pin_4
#define SERVO_PIN_TYPE GPIOC
#define SERVO_TIMER TIM1

#define MOT_DIRF_PIN GPIO_Pin_4
#define MOT_DIRB_PIN GPIO_Pin_0
#define MOT_DIRF_PIN_TYPE GPIOD
#define MOT_DIRB_PIN_TYPE GPIOC

#define MOT_PWML_PIN GPIO_Pin_5
#define MOT_PWMR_PIN GPIO_Pin_6
#define MOT_PWM_PIN_TYPE GPIOD
#define MOTOR_TIMER TIM2

#define BAT_VOLTAGE_PIN GPIO_Pin_1
#define BAT_VOLTAGE_PIN_TYPE GPIOA

#define LED_PIN GPIO_Pin_2
#define LED_PIN_TYPE GPIOA

#define PWM_PERIOD 1000

#define I2C_RX_ADDR (0x17<<1) // the real address is still 0x17 because of internal shifting - i.e. master still sends to slave on 0x17

void IIC_Init(u32 baudrate, u16 address){
    RCC_APB2PeriphClockCmd(RCC_APB2Periph_GPIOC, ENABLE);
    
    RCC_APB2PeriphClockCmd(RCC_APB2Periph_AFIO, ENABLE);
    RCC_APB1PeriphResetCmd(RCC_APB1Periph_I2C1, ENABLE);
    RCC_APB1PeriphResetCmd(RCC_APB1Periph_I2C1, DISABLE);
    RCC_APB1PeriphClockCmd(RCC_APB1Periph_I2C1, ENABLE);
    
    GPIO_InitTypeDef GPIO_InitStructure={0};
    GPIO_InitStructure.GPIO_Pin = SDA_PIN | SCL_PIN;
    GPIO_InitStructure.GPIO_Mode = GPIO_Mode_AF_OD;
    GPIO_InitStructure.GPIO_Speed = GPIO_Speed_30MHz;
    GPIO_Init(GPIOC, &GPIO_InitStructure);

    I2C_InitTypeDef I2C_InitTSturcture={0};
    I2C_InitTSturcture.I2C_ClockSpeed = baudrate;
    I2C_InitTSturcture.I2C_Mode = I2C_Mode_I2C;
    I2C_InitTSturcture.I2C_DutyCycle = I2C_DutyCycle_16_9;
    I2C_InitTSturcture.I2C_OwnAddress1 = address;
    I2C_InitTSturcture.I2C_Ack = I2C_Ack_Enable;
    I2C_InitTSturcture.I2C_AcknowledgedAddress = I2C_AcknowledgedAddress_7bit;
    I2C_Init(I2C1, &I2C_InitTSturcture);

    I2C_Cmd(I2C1, ENABLE);
}

void PWM_Init() {
    RCC_APB2PeriphClockCmd(RCC_APB2Periph_GPIOD | RCC_APB2Periph_GPIOC | RCC_APB2Periph_TIM1 | RCC_APB2Periph_AFIO, ENABLE);
    RCC_APB1PeriphClockCmd(RCC_APB1Periph_TIM2, ENABLE);
    
    GPIO_PinRemapConfig(GPIO_PartialRemap1_TIM1, ENABLE);
    GPIO_PinRemapConfig(GPIO_FullRemap_TIM2, ENABLE);

    GPIO_InitTypeDef GPIO_InitStructure = {0};
    GPIO_InitStructure.GPIO_Mode = GPIO_Mode_AF_PP;
    GPIO_InitStructure.GPIO_Speed = GPIO_Speed_30MHz;
    GPIO_InitStructure.GPIO_Pin = SERVO_CH1_PIN | SERVO_CH2_PIN | SERVO_CH3_PIN | SERVO_CH4_PIN;
    GPIO_Init(SERVO_PIN_TYPE, &GPIO_InitStructure);

    // Motor PWM pins: PD5 (MOT_PWML), PD6 (MOT_PWMR)
    GPIO_InitStructure.GPIO_Pin = MOT_PWML_PIN | MOT_PWMR_PIN;
    GPIO_Init(MOT_PWM_PIN_TYPE, &GPIO_InitStructure);

    TIM_TimeBaseInitTypeDef TIM_TimeBaseInitStructure={0};
    TIM_TimeBaseInitStructure.TIM_Period = PWM_PERIOD;
    TIM_TimeBaseInitStructure.TIM_Prescaler = 0;
    TIM_TimeBaseInitStructure.TIM_ClockDivision = TIM_CKD_DIV1;
    TIM_TimeBaseInitStructure.TIM_CounterMode = TIM_CounterMode_Up;
    TIM_TimeBaseInit(SERVO_TIMER, &TIM_TimeBaseInitStructure);
    TIM_TimeBaseInit(MOTOR_TIMER, &TIM_TimeBaseInitStructure);

    TIM_OCInitTypeDef TIM_OCInitStructure={0};
    TIM_OCInitStructure.TIM_OCMode = TIM_OCMode_PWM1; // Edge aligned
    TIM_OCInitStructure.TIM_OutputState = TIM_OutputState_Enable;
    TIM_OCInitStructure.TIM_Pulse = 0; // Start with 0% duty cycle
    TIM_OCInitStructure.TIM_OCPolarity = TIM_OCPolarity_High;

    TIM_OC1Init(SERVO_TIMER, &TIM_OCInitStructure);
    TIM_OC2Init(SERVO_TIMER, &TIM_OCInitStructure);
    TIM_OC3Init(SERVO_TIMER, &TIM_OCInitStructure);
    TIM_OC4Init(SERVO_TIMER, &TIM_OCInitStructure);

    TIM_OC1PreloadConfig(SERVO_TIMER, TIM_OCPreload_Enable);
    TIM_OC2PreloadConfig(SERVO_TIMER, TIM_OCPreload_Enable);
    TIM_OC3PreloadConfig(SERVO_TIMER, TIM_OCPreload_Enable);
    TIM_OC4PreloadConfig(SERVO_TIMER, TIM_OCPreload_Enable);

    TIM_OC3Init(MOTOR_TIMER, &TIM_OCInitStructure);  // PD6 (MOT_PWMR) - TIM2_CH3
    TIM_OC4Init(MOTOR_TIMER, &TIM_OCInitStructure);  // PD5 (MOT_PWML) - TIM2_CH4

    TIM_OC3PreloadConfig(MOTOR_TIMER, TIM_OCPreload_Enable);
    TIM_OC4PreloadConfig(MOTOR_TIMER, TIM_OCPreload_Enable);

    TIM_ARRPreloadConfig(SERVO_TIMER, ENABLE);
    TIM_ARRPreloadConfig(MOTOR_TIMER, ENABLE);
    TIM_CtrlPWMOutputs(SERVO_TIMER, ENABLE);
    //TIM_CtrlPWMOutputs(TIM2, ENABLE); // Not needed for TIM2
    TIM_Cmd(SERVO_TIMER, ENABLE);
    TIM_Cmd(MOTOR_TIMER, ENABLE);
}

void MOT_DIR_Init() {
    // Enable clocks for GPIOD and GPIOC
    RCC_APB2PeriphClockCmd(RCC_APB2Periph_GPIOD | RCC_APB2Periph_GPIOC, ENABLE);
    
    // Initialize MOT_DIRF_PIN (PD4) as GPIO output
    GPIO_InitTypeDef GPIO_InitStructure = {0};
    GPIO_InitStructure.GPIO_Pin = MOT_DIRF_PIN;
    GPIO_InitStructure.GPIO_Mode = GPIO_Mode_Out_PP;  // Push-pull output
    GPIO_InitStructure.GPIO_Speed = GPIO_Speed_30MHz;
    GPIO_Init(MOT_DIRF_PIN_TYPE, &GPIO_InitStructure);
    
    // Initialize MOT_DIRB_PIN (PC0) as GPIO output
    GPIO_InitStructure.GPIO_Pin = MOT_DIRB_PIN;
    GPIO_InitStructure.GPIO_Mode = GPIO_Mode_Out_PP;  // Push-pull output
    GPIO_InitStructure.GPIO_Speed = GPIO_Speed_30MHz;
    GPIO_Init(MOT_DIRB_PIN_TYPE, &GPIO_InitStructure);
    
    // Set initial direction (both LOW)
    GPIO_WriteBit(MOT_DIRF_PIN_TYPE, MOT_DIRF_PIN, Bit_RESET);
    GPIO_WriteBit(MOT_DIRB_PIN_TYPE, MOT_DIRB_PIN, Bit_RESET);
}

void PWM_SetDuty(TIM_TypeDef *timer, uint8_t channel, uint16_t duty_cycle) {
    if (duty_cycle > PWM_PERIOD) {
        duty_cycle = PWM_PERIOD;
    }

    switch (channel) {
        case 1:
            TIM_SetCompare1(timer, duty_cycle);
            break;
        case 2:
            TIM_SetCompare2(timer, duty_cycle);
            break;
        case 3:
            TIM_SetCompare3(timer, duty_cycle);
            break;
        case 4:
            TIM_SetCompare4(timer, duty_cycle);
            break;
    }
}

void PWM_SetFreq(TIM_TypeDef *timer, uint16_t frequency) {
    // Since SystemCoreClock is usually no more than 48MHz and PWM_PERIOD is equal to 1000, 
    // the max effective PWM frequency is 48000Hz. Trying to set the frequency to anything 
    // greater than this value will cap the value to 48000Hz.
    uint32_t prescaler = SystemCoreClock / (PWM_PERIOD * frequency);
    if(prescaler == 0) {
        prescaler = 1;
    }

    // According to the reference manual section 10.2.3 Counters and peripherals: 
    // "[...] the PSC is 16-bit and the actual dividing factor is equal to the value of R16_TIMx_PSC + 1."
    timer->PSC = (uint16_t)(prescaler-1);
    timer->SWEVGR = TIM_PSCReloadMode_Immediate;
}

int main(void) {
    NVIC_PriorityGroupConfig(NVIC_PriorityGroup_1);
    SystemCoreClockUpdate();
    Delay_Init();

    Delay_Ms(5);

    // Init pins
    MOT_DIR_Init();
    PWM_Init();

    // Init defaults for PWM timers
    PWM_SetFreq(SERVO_TIMER, 50);
    PWM_SetFreq(MOTOR_TIMER, 10000);

    IIC_Init(100000, I2C_RX_ADDR);
    I2C1->CTLR1 |= 0x0080; // CTLR1_NOSTRETCH_Set - Disable clock stretching
    I2C1->CTLR1 |= 0x0400; // CTLR1_ACK_Set - Enable ACK following each byte received - This also stops the clock stretching for each character received.
    // Thanks to Jim Merkle's code for those two lines above ^^: https://github.com/JimMerkle/CH32V003_I2C_Slave/blob/master/User/main.c
    // TODO: Try to get rid of those lines because they theoretically shouldn't be necassary but they are needed for I2C to work properly on my board. 

    uint8_t i2c_is_register_ok = 0;
    uint8_t i2c_bytes_read = 0;
    uint8_t i2c_register = 0;
    uint16_t i2c_data = 0;

    volatile uint16_t temp;
    (void)temp;

    while (1) {
        while(!I2C_CheckEvent(I2C1, I2C_EVENT_SLAVE_RECEIVER_ADDRESS_MATCHED));
    
        // Clear ADDR by reading the regs
        temp = I2C1->STAR1;
        temp = I2C1->STAR2;

        // TODO: add support for reading registers

        // Receive byte until STOP
        while (I2C_GetFlagStatus(I2C1, I2C_FLAG_STOPF) == RESET) {
            if (I2C_GetFlagStatus(I2C1, I2C_FLAG_RXNE) != RESET) {
                uint8_t data = I2C_ReceiveData(I2C1);
                
                if (!i2c_is_register_ok) {
                    i2c_register = data;
                    i2c_is_register_ok = 1;
                } else {
                    i2c_data |= (uint16_t)(data << (i2c_bytes_read * 8));
                    i2c_bytes_read += 1;
                }
            }
        }

        // Clear STOPF flag
        temp = I2C1->STAR1;
        I2C1->CTLR1 |= 0x0001;

        // Finish transfer and process the data (temporary solution for as long as there are no readable registers)
        if(i2c_bytes_read >= 2 && i2c_is_register_ok) {
            /// Available registers 
            // ID (DEC) | Access     | Data type | Description                           | Valid values
            // 1        | write-only | uint16_t  | TIM1 frequency                        | [1; 48000]
            // 2        | write-only | uint16_t  | TIM2 frequency                        | [1; 48000]
    
            // 4        | write-only | uint16_t  | TIM1 CH1 duty cycle (Servo CH1 PWM)   | [0; PWM_PERIOD)
            // 5        | write-only | uint16_t  | TIM1 CH2 duty cycle (Servo CH2 PWM)   | [0; PWM_PERIOD)
            // 6        | write-only | uint16_t  | TIM1 CH3 duty cycle (Servo CH3 PWM)   | [0; PWM_PERIOD)
            // 7        | write-only | uint16_t  | TIM1 CH4 duty cycle (Servo CH4 PWM)   | [0; PWM_PERIOD)

            // 10       | write-only | uint16_t  | TIM2 CH3 duty cycle (Right Motor PWM) | [0; PWM_PERIOD)
            // 11       | write-only | uint16_t  | TIM2 CH4 duty cycle (Left Motor PWM)  | [0; PWM_PERIOD)

            // 12       | write-only | uint16_t  | Motor direction: (DIRF | (DIRB << 8)) | {0, 1, (1 << 8), 1 | (1 << 8) }

            switch (i2c_register) {
                case 1: 
                    PWM_SetFreq(TIM1, i2c_data);
                    break;

                case 2: 
                    PWM_SetFreq(TIM2, i2c_data);
                    break;

                case 4: 
                case 5: 
                case 6:
                case 7: 
                    PWM_SetDuty(TIM1, i2c_register - 4 + 1, i2c_data);
                    break;

                case 10: 
                case 11: 
                    PWM_SetDuty(TIM2, i2c_register - 8 + 1, i2c_data);
                    break;

                case 12: 
                    GPIO_WriteBit(MOT_DIRF_PIN_TYPE, MOT_DIRF_PIN, i2c_data & 1);
                    GPIO_WriteBit(MOT_DIRB_PIN_TYPE, MOT_DIRB_PIN, (i2c_data >> 8) & 1);
                    break;

                default: 
                    // do nothing
                    break;
            }

            // Return to the default state
            i2c_is_register_ok = 0;
            i2c_bytes_read = 0;
            i2c_register = 0;
            i2c_data = 0;
        }
    }
}

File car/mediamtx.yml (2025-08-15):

###############################################
# Global settings

# Settings in this section are applied anywhere.

###############################################
# Global settings -> General

# Verbosity of the program; available values are "error", "warn", "info", "debug".
logLevel: info
# Destinations of log messages; available values are "stdout", "file" and "syslog".
logDestinations: [stdout]
# If "file" is in logDestinations, this is the file which will receive the logs.
logFile: mediamtx.log
# If "syslog" is in logDestinations, use prefix for logs.
sysLogPrefix: mediamtx

# Timeout of read operations.
readTimeout: 10s
# Timeout of write operations.
writeTimeout: 10s
# Size of the queue of outgoing packets.
# A higher value allows to increase throughput, a lower value allows to save RAM.
writeQueueSize: 512
# Maximum size of outgoing UDP packets.
# This can be decreased to avoid fragmentation on networks with a low UDP MTU.
udpMaxPayloadSize: 1472

# Command to run when a client connects to the server.
# This is terminated with SIGINT when a client disconnects from the server.
# The following environment variables are available:
# * MTX_CONN_TYPE: connection type
# * MTX_CONN_ID: connection ID
# * RTSP_PORT: RTSP server port
runOnConnect:
# Restart the command if it exits.
runOnConnectRestart: no
# Command to run when a client disconnects from the server.
# Environment variables are the same of runOnConnect.
runOnDisconnect:

###############################################
# Global settings -> Authentication

# Authentication method. Available values are:
# * internal: users are stored in the configuration file
# * http: an external HTTP URL is contacted to perform authentication
# * jwt: an external identity server provides authentication through JWTs
authMethod: internal

# Internal authentication.
# list of users.
authInternalUsers:
  # Default unprivileged user.
  # Username. 'any' means any user, including anonymous ones.
- user: any
  # Password. Not used in case of 'any' user.
  pass:
  # IPs or networks allowed to use this user. An empty list means any IP.
  ips: []
  # List of permissions.
  permissions:
    # Available actions are: publish, read, playback, api, metrics, pprof.
  - action: publish
    # Paths can be set to further restrict access to a specific path.
    # An empty path means any path.
    # Regular expressions can be used by using a tilde as prefix.
    path:
  - action: read
    path:
  - action: playback
    path:

  # Default administrator.
  # This allows to use API, metrics and PPROF without authentication,
  # if the IP is localhost.
- user: any
  pass:
  ips: ['127.0.0.1', '::1']
  permissions:
  - action: api
  - action: metrics
  - action: pprof

# HTTP-based authentication.
# URL called to perform authentication. Every time a user wants
# to authenticate, the server calls this URL with the POST method
# and a body containing:
# {
#   "user": "user",
#   "password": "password",
#   "ip": "ip",
#   "action": "publish|read|playback|api|metrics|pprof",
#   "path": "path",
#   "protocol": "rtsp|rtmp|hls|webrtc|srt",
#   "id": "id",
#   "query": "query"
# }
# If the response code is 20x, authentication is accepted, otherwise
# it is discarded.
authHTTPAddress:
# Actions to exclude from HTTP-based authentication.
# Format is the same as the one of user permissions.
authHTTPExclude:
- action: api
- action: metrics
- action: pprof

# JWT-based authentication.
# Users have to login through an external identity server and obtain a JWT.
# This JWT must contain the claim "mediamtx_permissions" with permissions,
# for instance:
# {
#  ...
#  "mediamtx_permissions": [
#     {
#       "action": "publish",
#       "path": "somepath"
#     }
#   ]
# }
# Users are expected to pass the JWT in the Authorization header or as a query parameter.
# This is the JWKS URL that will be used to pull (once) the public key that allows
# to validate JWTs.
authJWTJWKS:
# name of the claim that contains permissions.
authJWTClaimKey: mediamtx_permissions

###############################################
# Global settings -> Control API

# Enable controlling the server through the Control API.
api: no
# Address of the Control API listener.
apiAddress: :9997
# Enable TLS/HTTPS on the Control API server.
apiEncryption: no
# Path to the server key. This is needed only when encryption is yes.
# This can be generated with:
# openssl genrsa -out server.key 2048
# openssl req -new -x509 -sha256 -key server.key -out server.crt -days 3650
apiServerKey: server.key
# Path to the server certificate.
apiServerCert: server.crt
# Value of the Access-Control-Allow-Origin header provided in every HTTP response.
apiAllowOrigin: '*'
# List of IPs or CIDRs of proxies placed before the HTTP server.
# If the server receives a request from one of these entries, IP in logs
# will be taken from the X-Forwarded-For header.
apiTrustedProxies: []

###############################################
# Global settings -> Metrics
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

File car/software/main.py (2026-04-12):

import sys, traceback
import time
import asyncio
from websockets.asyncio.server import serve
import math
import control
import vision
import threading
import http.server

async def main_remote_control():
    def run_http_server():
        server = http.server.HTTPServer(('0.0.0.0', 8000), http.server.SimpleHTTPRequestHandler)
        server.serve_forever()
    
    http_thread = threading.Thread(target=run_http_server, daemon=True)
    http_thread.start()
    
    control.start()
    controlloop = asyncio.create_task(control.control_loop())

    async def serve_callback(websocket):
        async for message in websocket:
            parts = message.split()
            if parts[0] == "steer":
                control.set_steer_target(float(parts[1]))
            elif parts[0] == "motors":
                control.set_drive_target(float(parts[1]))
            elif parts[0] == "motorfreq":
                control.pcb.set_timer_frequency(control.pcb.PWM_MOTOR_TIMER, int(parts[1]))
                
            print(parts)
    
    async with serve(serve_callback, "0.0.0.0", 8080) as server:
        await server.serve_forever()
    
    await controlloop

def main_vision():
    vision.init_camera()
    
    while True:
        marker = vision.locate_marker()
        if marker != None:
            mx, my = marker
            halfx = 1280.0 / 2.0
            halfy = 720.0 / 2.0
            if mx > halfx:
                control.steer((mx - halfx) / halfx * control.MAX_STEER_ANGLE)
            else:
                control.steer((mx - halfx) / halfx * control.MAX_STEER_ANGLE)

            control.drive(my / 720.0 * 100.0)
        else:
            control.drive(0.0)
            
        time.sleep(0.1)

def main_test():
    t = 0.0
    while True:
        control.steer(math.sin(3.1415926 * t)*30.0)
        time.sleep(0.05)
        t += 0.05

if __name__ == "__main__":
    try:
        match sys.argv[-1]:
            case 'vision':
                print("Running the \"Vision\" main loop")
                main_vision()
            case 'test':
                print("Running the \"Test\" main loop")
                main_test()
            case _:
                print("Running the \"Remote Control\" main loop")
                asyncio.run(main_remote_control())
 
    except KeyboardInterrupt:
        print("\nShutdown requested...exiting")
    except Exception:
        traceback.print_exc(file=sys.stdout)
    
    control.stop()
    sys.exit(0)

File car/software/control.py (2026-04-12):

import time
from pcb_driver import PCBDriver
import threading
import asyncio

control_lock = threading.Lock()

FILTERING_ENABLE = True
TIMESTEP = 0.02

# Max servo rotational speed in degrees/s
MAX_STEER_CHANGE_RATE = 270.0
steer_target = 0.0
steer_current = 0.0

# Max motor speed change in percent/s
MAX_DRIVE_CHANGE_RATE = 200.0
drive_target = 0.0
drive_current = 0.0

MIN_PULSE_MS = 0.5
MAX_PULSE_MS = 2.5
MAX_STEER_ANGLE = 30.0
PIN_FORWARD = 6
PIN_BACKWARD = 5

pcb = PCBDriver()

def set_steer_target(angle: float):
    global control_lock, steer_target
    
    if not FILTERING_ENABLE:
        steer(angle)    
    else:
        with control_lock:
            steer_target = angle
        
def set_drive_target(val: float):
    global control_lock, drive_target
    
    if not FILTERING_ENABLE:
        drive(val)
    else:    
        with control_lock:
            drive_target = val

# angle: [0.0, 180.0], 0.0 == left, 90.0 == center, 180.0 == right
# returns [MIN_PULSE_MS, MAX_PULSE_MS]
def servo_val(angle: float) -> float:
    angle = max(0.0, min(180.0, angle))
    return (MIN_PULSE_MS + (angle / 180.0) * (MAX_PULSE_MS - MIN_PULSE_MS))

# angle: [-MAX_STEER_ANGLE, MAX_STEER_ANGLE], positive values turn to the right
def steer(angle: float):
    global pcb

    angle = max(-MAX_STEER_ANGLE, min(MAX_STEER_ANGLE, angle))
    
    val = pcb.PWM_MAX_DUTY * servo_val(90.0+angle) / (1000.0/50.0) #20ms

    pcb.set_ch_duty(pcb.PWM_SERVO_TIMER, 1, int(val))
    
def drive(val: float):
    global pcb

    adj = int(val / 100.0 * pcb.PWM_MAX_DUTY)

    if val > 0.0:
        pcb.set_motor_direction(1)
        pcb.set_ch_duty(pcb.PWM_MOTOR_TIMER, pcb.PWM_RIGHT_MOTOR_CH, adj)
        pcb.set_ch_duty(pcb.PWM_MOTOR_TIMER, pcb.PWM_LEFT_MOTOR_CH, adj)
    elif val == 0.0:
        pcb.set_motor_direction(0)
        pcb.set_ch_duty(pcb.PWM_MOTOR_TIMER, pcb.PWM_RIGHT_MOTOR_CH, 0)
        pcb.set_ch_duty(pcb.PWM_MOTOR_TIMER, pcb.PWM_LEFT_MOTOR_CH, 0)
    else:
        pcb.set_motor_direction(-1)
        pcb.set_ch_duty(pcb.PWM_MOTOR_TIMER, pcb.PWM_RIGHT_MOTOR_CH, -adj)
        pcb.set_ch_duty(pcb.PWM_MOTOR_TIMER, pcb.PWM_LEFT_MOTOR_CH, -adj)

def start():
    pcb.set_timer_frequency(pcb.PWM_SERVO_TIMER, 50)
    pcb.set_timer_frequency(pcb.PWM_MOTOR_TIMER, 12000)
    steer(0.0)
    drive(0.0)

def stop():
    pcb.set_ch_duty(pcb.PWM_SERVO_TIMER, 1, 0)
    pcb.set_ch_duty(pcb.PWM_SERVO_TIMER, 2, 0)
    pcb.set_ch_duty(pcb.PWM_MOTOR_TIMER, 3, 0)
    pcb.set_ch_duty(pcb.PWM_MOTOR_TIMER, 4, 0)
    
    pcb.set_ch_duty(pcb.PWM_MOTOR_TIMER, pcb.PWM_RIGHT_MOTOR_CH, 0)
    pcb.set_ch_duty(pcb.PWM_MOTOR_TIMER, pcb.PWM_LEFT_MOTOR_CH, 0)

# Returns v so that: -m <= v <= m
def clamp_margin(v: float, m: float) -> float:
    return min(m, max(-m, v))

# run with asyncio
async def control_loop():
    global control_lock
    global steer_target, steer_current
    global drive_target, drive_current
    
    if not FILTERING_ENABLE:
        return
    
    while True:
        with control_lock:
            steer_current += clamp_margin(steer_target - steer_current, MAX_STEER_CHANGE_RATE * TIMESTEP)
            drive_current += clamp_margin(drive_target - drive_current, MAX_DRIVE_CHANGE_RATE * TIMESTEP)
            #print(steer_current, drive_current)
            
            steer(steer_current)
            drive(drive_current)
            
        await asyncio.sleep(TIMESTEP)

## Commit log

2025-08-15 New frame and mAntPWM CH32V003 board
    [RaspberryPi5.step, picar.3mf, picar.f3d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]
2025-11-05 PCB Main Board Design
    [pcb_main_board.kicad_pcb, pcb_main_board.kicad_sch]
2025-11-07 List of Mouser footprints
2026-01-24 V3 Early Upload
    The software doesn't work yet
    [pcb_main_board.step, pcb_main_board.stl]
2026-01-24 Fix schematic in the README
2026-04-12 V3 firmware, software and better README
    [pcb_main_board.kicad_pcb, pcb_main_board.kicad_sch, pcb_main_board.step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]
2026-04-12 Fix pcb schematic svg
2026-06-27 Began working on the final PCB revision
    [pcb_main_board.kicad_pcb, pcb_main_board.kicad_sch, pcb_main_board.step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]
